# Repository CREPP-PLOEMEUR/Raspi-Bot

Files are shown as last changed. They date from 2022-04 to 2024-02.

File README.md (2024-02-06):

<!--# RaspiBot -->
<!--+ 2016-2017 -->
<!--$ Python-->
<!--$ Arduino -->
<!--$ Bluetooth -->

<!--% Un robot avec retour vidéo et contrôle par Bluetooth -->

# RaspiBot

Un robot avec retour vidéo et contrôle par Bluetooth

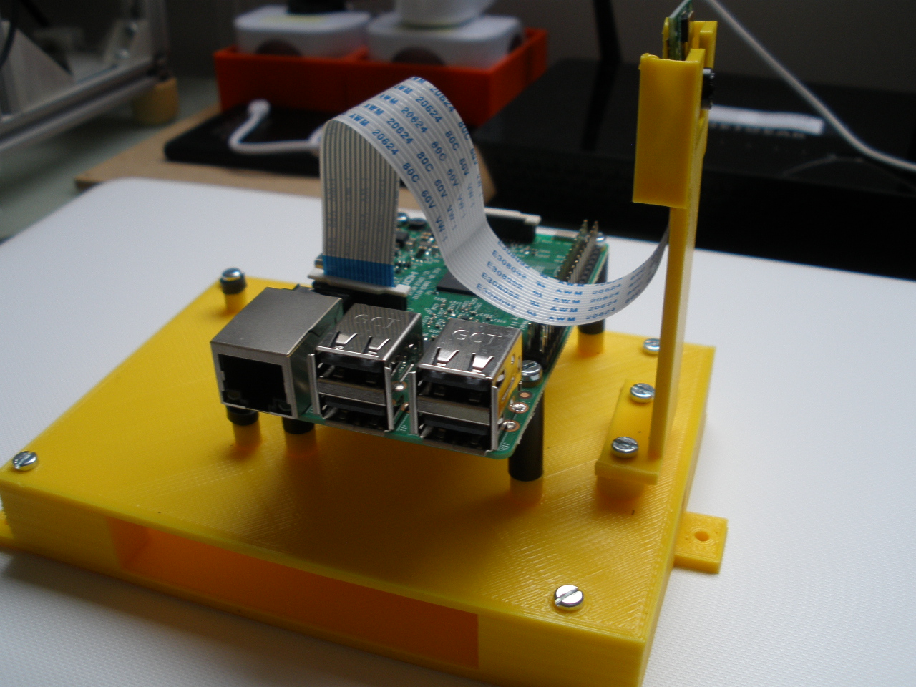
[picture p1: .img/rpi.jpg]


## Sommaire

- Caméra : Toutes les informations sur la caméra et son contrôle

- Code_Arduino : Le code du robot avec les bibliothèques Arduino

- Code_essais : Les codes d'essais des moteurs, caméra...

- Fichiers TSL : Les fichiers STL du projet

- Images : Les images du projet

- Instructions : Les instructions du montage du robot

- Moteurs : les instructions et calculs pour le dimensionnement des moteurs

- 

## Liste du matériel

- 1 ordinateur embarqué Raspberry Pi3 Modèle B 1GB
- 1 Alimentation Micro USB 5V 2,5A pour Raspberry Pi3 et power bank
- 1 Power bank Li-polymer 10000 mAh sorties 1 et 2,1A pour alimentation Rpi3 en autonome
- 1 Module caméra 5MP pour Raspberry Pi3
- 1 carte mémoire microSDHC SanDisk 16 Go, Classe 10

- 1 ensemble support pour Rpi3, carte Arduino et caméra en PLA jaune ( avec visserie et entretoises )

## Informations pratiques

- L'ensemble support avec son Rpi3, sa carte Arduino, sa caméra et la batterie « power bank » sera par la suite intégré au robot roulant.

- La batterie power bank s'insère dans l'espace sous le Rpi3 – carte Arduino. Elle assure l'alimentation de l'ensemble Rpi3-carte Arduino-caméra pour assurer l'autonomie du robot roulant. Son utilisation sera vue par la suite.

- Le support de caméra est provisoire, il sert uniquement à assurer un positionnement en toute sécurité de la caméra pendant les essais.

- Installation de la caméra :

    - Insérer le circuit imprimé dans son support, la nappe vers le bas. 
    - Le connecteur de la carte est celui entre la prise son et la prise hdmi ,noté caméra sur la carte,
    - Relever avec précaution le bloqueur blanc, il se relève de quelques millimètres,
    - Insérer la nappe, contacts vers la prise hdmi, partie bleue vers le port RJ45
    - Ré appuyer sur le bloqueur pour bien fixer.

- L'alimentation ( chargeur ) est utilisée pour alimenter le Rpi3 pour la prise en main du Rpi3 ( installation du logiciel d'exploitation, configuration, chargements des logiciels permettant la prise de contrôle à distance du Rpi3 et du contrôle des flux vidéo sur l'ordinateur distant ).

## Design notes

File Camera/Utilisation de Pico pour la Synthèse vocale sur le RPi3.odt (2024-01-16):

UTILISATION de PICO pour la SYNTHESE VOCALE sur le RPi3

1°- Installer sox :

* Dans le Terminal du RPi3 taper sudo apt-get install sox

2°- Installer Pico :

* Dans le gestionnaire de paquets Synaptic j'ai trouvé libttspico-utils déjà installé.

Quand vous allez dans les propriétés de ce paquet il est dit :

The svox Pico engine is a software speech synthesizer for German, English ( GB and US ), Spanish, French and Italian.

3°- J'ai inséré le scrip en bash suivant écrit par Nicolas dans un fichier lyrics placé dans le dossier Music du RPi3

#!/bin/bash

var="$*"

echo $var

pico2wave -l=fr-FR -w=.fichier.wav "$var" && play .fichier.wav

rm /home/pi/.fichier.wav

4°- Dans le Terminal du RPi3 je tape les cdes suivantes :

a- sudo cp /home/pi/Music/lyrics /bin

b- sudo chmod 777 /bin/lyrics

Puis après avoir mis en service votre émission son sur le RPi3 taper la cde suivante dans le Terminal :

c- lyrics « Ceci est un son généré par Pico »

« Ceci est un son généré par Pico » est appellé « argument ». L'argument peut-être n'importe quelle phrase.

Information :

Il est possible de trouver dans un Carrefour Market des mini HP Bluetooth ( vue par Patrick Pastor ) marque BLUESKY coût : 6,90 €

- Sortie audio 1x1,5w RMS

- Alimentation 5vcc 500mA

- Batterie 3,7vcc 250mAh Lithium-ion

- Autonomie jusqu'à 3,5h

- Temps de recharge minimum 2h environ ( port USB de votre ordinateur )

-Portée du Bluetooh jusqu'à 9,7 m

- Entrée filaire AUX 3,5 mm

Il doit être possible de trouver l'équivalent dans d'autres magasins.

=-=-=-=-=-=

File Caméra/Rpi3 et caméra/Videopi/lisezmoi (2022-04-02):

les vidéos se lancent à l'aide de leurs fichiers .sh respectifs

L'interface mainvideoZ7.py ne sert qu'à en modifier les parametres si cela s'avere necessaire

Ne pas oublier de vérifier pour les fichiers sh ,dans "propriétés/permissions" que la case "autoriser l'execution du fichier comme un programme est bien cochée

même chose pour le fichier d'interface MainvideoZ7.py

Le fichier MainvideoZ7.py se lance avec "executer"

Les fichiers .sh se lancent avec "lancer dans un terminal"

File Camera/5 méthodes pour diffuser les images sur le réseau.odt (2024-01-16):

MagdiBlog

Parce que si on ne se compliquait pas un peu la vie, ce serait beaucoup moins drôle !

MagdiBlog

Aller au contenu

Accueil Sommaire Projets

Pi Home Dash Screen

Pi Car Jukebox

Pi Time Lapse

Pi BOA Drone

BOA Pi Secure Gateway

Domotique GPIO Divers Contact Liens A propos

Magdiblog

Mon CV

RSS

Raspberry Pi Camera – 5 façons de faire du streaming

47 réponses

IMG_8806Le module Raspberry Pi Camera (et la version sans filtre IR, le module NoIR) sont de petits circuits (2,5cm x 2,5cm) dotés d’un capteur photo de 2592 x 1944 pixels capable d’enregistrer en 1080p à 30 images par secondes (ou 60 fps en 720p). Ce module se branche directement sur le port CSI du Pi prévu à cet effet.

La version NoIR permet de voir les infra-rouge, ce qui autorisera une vision nocturne si on le couple à un projecteur infra-rouge comme expliqué à fin de cet article : Système de vidéo-surveillance abordable avec des Raspberry Pi

Que ce soit pour un système de vidéo surveillance ou pour le pilotage d’un robot à distance, il faut pouvoir récupérer le flux vidéo et le diffuser à travers le réseau (streaming). Nous allons voir dans cet article 5 méthodes pour diffuser le flux vidéo d’un module Raspberry Pi Camera, plus ou moins efficacement.

Introduction et matériel utilisé

Le module Raspberry Pi Camera étant branché directement sur un Raspberry Pi, si vous voulez pouvoir voir les images capturées depuis un autre endroit qu’un écran branché sur ce même Pi, vous allez devoir envoyer ces images à travers le réseau. De nombreuses utilisations sont possibles :

la caméra de surveillance que l’on souhaite observer depuis son smartphone quand on part en vacance

le robot que l’on souhaite piloter à distance depuis un ordinateur de contrôle

filmer et diffuser des images en direct à travers internet

etc…

Petit bémol sur la notion de « streaming » vidéo : En principe, lorsqu’on parle de streaming vidéo, il s’agit bien d’un flux vidéo diffusé en direct. Comme nous allons le voir plus loin dans cet article, cette méthode consomme énormément de ressources (notamment en terme de bande passante), et dans de nombreux cas, il sera plus judicieux de diffuser une « suite d’images » à intervalles réguliers.

IMG_8810Le matériel

Pour l’ensemble des méthodes exposées dans cet article, nous utiliserons le matériel et le montage suivant :

Raspberry Pi A+

Module Camera ou la version NoIR

Un dongle WiFi Netgear WNA1000M

Une carte micro-SD SanDisk 8Go

Une batterie Romoss 5200mAh

Le Raspberry Pi A+ est vraiment idéal pour ce genre projet. Découvrez pourquoi en lisant cet article : Raspberry Pi A+ : Le meilleur de tous

On installe une Raspbian, tout ce qu’il y a de plus standard, on se connecte à son réseau WiFi et on active le module caméra grâce à l’outil raspi-config.

Voyons maintenant comment diffuser les images sur le réseau.

Méthode 1 : Netcat et Mplayer

C’est la méthode la plus simple et la plus directe. Il s’agit simplement de rediriger le flux capturé par la commande raspivid dans netcat, puis de récupérer ce flux et l’injecter en entrée dans le lecteur vidéo Mplayer. L’inconvénient de cette méthode est que le flux vidéo n’est visible que depuis un seul PC distant.

Depuis un PC sous Linux exécutez dans un premier temps la commande suivante (après avoir installé mplayer si besoin) :

nc -l -p 5001 | /usr/bin/mplayer -fps 10 -cache 1024 -

Cette commande ordonne à nc (netcat) d’écouter sur le port 5001 et redirige ce qui arrive dans le lecteur vidéo Mplayer en prévoyant un cache de 1024 Ko pour 10 images par secondes.

Puis, sur le Pi, il suffit d’exécuter raspivid et de rediriger la sortie vers l’adresse IP de notre PC client en utilisant netcat :

raspivid -t 0 -w 1280 -h 720 -o - | nc adresse_ip_du_pc_client 5001

On indique ainsi à raspivid de capturer des images en 1280×720 pixels et de les envoyer à netcat.

Simple et efficace, une fenêtre Mplayer s’ouvre automatiquement sur le PC client avec les images en direct. On notera toutefois une forte latence qui peut varier de 3 à 15 secondes en fonction de la qualité et du nombre d’images transmisses et de la qualité du lien WiFi.

Note : Un test réalisé sur un Raspberry Pi B, branché en Ethernet, permet de réduire la latence à environ une seconde.

Si vous souhaitez enregistrer le flux vidéo dans un fichier sur le PC client, il suffit de modifier la première commande de cette manière :

nc -l -p 5001 | /usr/bin/mplayer -fps 10 -cache 1024 -demuxer h264es -dumpstream -dumpfile ./Bureau/ma_video.h264 -

Méthode 2 : streaming VLC

Cette méthode, relativement simple à mettre en place, souffre d’une très forte latence. Toutefois, et contrairement à la première méthode, le flux vidéo est visible depuis plusieurs postes clients.

Sur le Pi, il suffit d’installer VLC :

apt-get install vlc

Puis de rediriger la sortie de la commande raspivid (comme dans la méthode 1) vers VLC en exécutant la commande suivante :

raspivid -t 0 -n --width 1280 --height 720 -o - | cvlc stream:///dev/stdin --sout '#standard{access=http,mux=ts,dst=:8090}' :demux=h264

Coté PC client, il suffit de lire le flux vidéo avec VLC grâce à la commande :

cvlc http://adresse_ip_du_pi:8090

Pour enregistrer le flux vidéo dans un fichier, utilisez la commande suivante :

cvlc http://adresse_ip_du_pi:8090 --sout file/ts:./Bureau/ma_video.h264

Cette méthode est à privilégier si vous souhaitez diffuser votre flux vidéo à plusieurs personnes sur internet par exemple, et que la latence n’est pas un problème.

Méthode 3 : streaming de Pi à Pi avec OMXplayer

Les méthodes 1 et 2 permettent de diffuser le flux vidéo à destination d’un ordinateur distant. Si vous souhaitez capturer un flux vidéo depuis un Pi pour l’observer depuis un autre Pi branché à un écran, il convient d’utiliser le lecteur OMXplayer.

Cette méthode est un peu plus complexe à mettre en oeuvre mais permet plus de souplesse quant à l’usage que l’on souhaite en faire. Depuis le Pi équipé du module caméra, nous allons procéder exactement comme pour la méthode 1, en redirigeant la sortie de la commande raspivid dans netcat. Puis, sur le Pi branché à l’écran de visionnage, nous allons dans un premier temps récupérer le flux netcat pour l’enregistrer dans un fichier et le lire, dans un deuxième temps, avec OMXplayer.

Sur le Pi de visionnage, créez d’abord un fichier de type fifo :

mkfifo /dev/shm/video.fifo

Deux points très important à comprendre dans cette commande :

/dev/shm : ce point montage fonctionne comme un disque dur mais aucune donnée ne sera stockée sur le disque dur en lui même ; tout sera géré en mémoire vive. C’est parfait pour y placer un fichier vidéo tampon.

fichier de type .fifo : les fichiers de type fifo fonctionnent comme les fichiers standards, mais se comportent comme des « pipes », ce qui permet au système d’y stocker des données sans passer par le système de fichier. Encore une fois, parfait pour y placer un fichier vidéo tampon 🙂

Le fichier tampon étant prêt, il faut maintenant le remplir. Côté Pi de visionnage, mettez netcat en écoute en redirigeant la sortie vers le fichier tampon :

nc -l -p 5001 > /dev/shm/video.fifo

Puis côté Pi caméra, envoyez le flux vidéo à travers netcat comme dans la méthode 1 :

raspivid -t 0 -w 960 -h 540 -o - | nc adresse_ip_du_pi_visionnage 5001

De retour sur le Pi de visionnage, il suffit de dire à OMXplayer de lire le fichier tampon :

omxplayer /dev/shm/video.fifo

Cette méthode n’offre pas une latence exemplaire, mais permet de transmettre un flux vidéo de Pi à Pi. Idéal par exemple pour créer un portier vidéo, avec un Pi qui film et un Pi qui affiche la vidéo, les deux Pi étant reliés par WiFi 🙂

Méthode 4 : mjpg-streamer

A partir de là, on sort du streaming vidéo pur et dur puisqu’il s’agit, avec le mjpeg, de transmettre et d’afficher une suite de photos les unes après les autres. Le résultat est beaucoup moins fluide puisqu’on ne pourra espérer afficher que 5 à 10 images par seconde maximum (contre 10 à 30 images par secondes pour les méthodes précédentes), mais nous pourrons exploiter les images beaucoup plus simplement en les affichant dans une page web, ou sur un écran comme le PiHomeDashScreen par exemple. Si vous disposez d’un NAS Synology, ou d’un système sachant gérer des caméras IPs, vous pourrez également exploiter la caméra du Pi grâce à cette méthode.

Voici le lien vers la page SourceForge de mjpg-streamer : http://sourceforge.net/projects/mjpg-streamer/

Dans un premier temps, installez les dépendances de mjpg-streamer ainsi que subversion :

apt-get install subversion

libv4l-dev

libjpeg8-dev

imagemagick

mjpg-streamer aura besoin d’un fichier videodev.sh pour fonctionner correctement :

ln -s /usr/include/linux/videodev2.h /usr/include/linux/videodev.h

Téléchargez ensuite la dernière version de mjpg-streamer grâce à subversion, puis installez le en utilisant les commandes suivantes :

svn co https://svn.code.sf.net/p/mjpg-streamer/code/

cd code/mjpg-streamer

make USE_LIBV4L2=true clean all

make DESTDIR=/usr install

Une fois installé, créez un répertoire temporaire et lancez raspistill en mode timelapse pour capturer 2 images par secondes :

mkdir /tmp/stream

raspistill --nopreview -w 640 -h 480 -q 5 -o /tmp/stream/pic.jpg -tl 500 -t 9999999

Enfin, lancez mjpg-streamer grâce à cette commande :

LD_LIBRARY_PATH=/usr/local/lib mjpg_streamer -i "input_file.so -f /tmp/stream -n pic.jpg" -o "output_http.so -w ./www"

Par défaut, mjpg-streamer lancera un serveur web sur le port 8080/TCP auquel vous pouvez accéder avec un navigateur en utilisant l’adresse : http://adresse_du_pi:8080

Vous devriez voir l’interface de démonstration de mjpg-streamer :

capture_mjpg-streamer

Les deux options les plus intéressantes sont JavaScript et Stream. Ces deux méthodes vous permettrons de récupérer les images pour les afficher dans une page web, ou sur le PiHomeDashScreen comme vous pouvez le voir dans la photo si dessous :

capture_homedashscreen_pi_camera

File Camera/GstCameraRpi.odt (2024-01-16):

# GST :

## commande sur RPI3 IP 192.168.0.29 avec caméra:

/opt/vc/bin/raspivid -t 0 -hf -fps 20 -w 300 -h 300 -o - | gst-lunch-1.0 fdsrc ! h264parse ! rtph264pay config-interval=1 pt=96 ! gdppay ! tcpserversink host=192.168.1.11 port=5000

commande sur Ubuntu :

gst-launch-1.0 -v tcpclientsrc host=192.168.1.11 port=5000 ! gdpdepay ! rtph264depay ! avdec_h264 ! videoconvert ! autovideosink sync=false

commande sur Apple MacBook OS Sierra :

gst-launch-1.0 -v tcpclientsrc host= 192.168.0.29 port=5000 ! gdpdepay ! rtph264depay ! avdec_h264 ! videoconvert ! osxvideosink sync=false

## difficultés rencontrées :

1. Linux Ubuntu 16.04 : aucune !
2. Apple MacBook : installation par brew sous Terminal des paquets suivants :
  1. brew install gstreamer et vérification ok par gst-inspect-1.0 (si problème avec le Python natif Apple, brew unlink python / brew link –overwrite python/ brew install gstreamer)
  2. brew install gst-plugins-base
  3. brew install gst-libav
  4. brew install gst-plugins-ugly
  5. brew install gst-plugins-bad
  6. brew install gst-plugins-good
3. impossible de lire le flux gst sur Apple MacBook VLC

(peut-être que pour Microsoft Windows,

mplayer -fps 200 -demuxer h264es ffmpeg://tcp://192.168.0.29:5000

et il faudra peut-être installer plusieurs bibliothèques complémentaires

## impressions

très rapide, pas de latence

# SON

Achat d'un petit haut parleur Bluetooth + fil à Carrefour Ploemeur : moins de 9€ !

pico2wave -l fr-FR -w bonjour.wav « Bonjour le monde »

installation de sox :

sudo apt-get install sox

Terminal/ ligne de commande :

play bonjour.wav

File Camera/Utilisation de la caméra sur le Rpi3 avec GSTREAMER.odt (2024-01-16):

UTILISATION de la CAMÉRA sur le RPi3 avec GSTREAMER

1°- Installer GSTREAMER sur le RPi3 et son PC client :

* Aller dans Gestionnaire de paquets Synaptic

* Rechercher gstreamer1.0

Ensuite, comme je n'y connais pas grand chose, j'ai installé tous les paquets en commençant par :

gstreamer1.0-alsa ….les spécialistes sauront faire leur choix.

2°- Dans un fichier ad hoc sauvegardé sur le bureau du RPi3, écrire la cde suivante que l'on appellera « Commande émission caméra » ( origine Patrick Pastor ) :

/opt/vc/bin/raspivid -t 0 -hf -fps 20 -w 300 -h 300 -o - | gst-launch-1.0 fdsrc ! h264parse ! rtph264pay config-interval=1 pt=96 ! gdppay ! tcpserversink host= adresse IP du RPi3 port=5000

3°- Dans un fichier ad hoc sauvegardé sur le bureau du Pc client, écrire la cde suivante que l'on appellera « Commande réception image » ( origine Patrick Pastor ) :

gst-launch-1.0 -v tcpclientsrc host= adresse IP du Rpi3 port=5000 ! gdpdepay ! rtph264depay ! avdec_h264 ! videoconvert ! autovideosink sync=false

4°- Mise en œuvre :

* Après avoir pris le contrôle du RPi3 par le Pc client :

a- Copier-coller dans le Terminal du RPi3 la ligne de cde du fichier ad hoc. La diode rouge de la caméra s'allume, la caméra est en service.

b- Copier-coller dans le Terminal du Pc client la ligne de cde du fichier ad hoc,

c- Taper Enter ( clavier du PC client ) L'écran de la caméra s'affiche sur le bureau du Pc client.

* Si l'on souhaite modifier les dimensions de cet écran, intervenir dans la ligne de cde émission caméra du Rpi3 au niveau de -w et -h,

* On peut également agir sur le nombre d'images par seconde au niveau de -fps.

Remarques :

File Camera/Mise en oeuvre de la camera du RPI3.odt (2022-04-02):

MISE en OEUVRE de la CAMÉRA du Rpi3

RPi3 sous Jessie (Debian) et PC client sous Linux

=-=-=-=-=-=-=

MÉTHODE GSTREAMER :

I- Installer gstreamer1.0 dans le Rpi3 et le PC client :

* Ouvrir Synaptic ( si ce gestionnaire de paquets n'est pas installé taper dans les Terminaux du Rpi3 et du PC client ) sudo apt-get install synaptic

* Si Synaptic est installé, dans les Terminaux taper sudo apt-get update

- Cliquer sur Rechercher,

- Dans la fenêtre qui apparaît taper gstreamer1.0 puis cliquer sur Rechercher,

- Dans la liste des paquets qui apparaît, les paquets déjà installés sont signalés par un petit carré vert,

- Les paquets suivants doivent être installés de façon exhaustive :

- gstreamer1.0-alsa

- gstreamer1.0-clutter-3.0

- gstreamer1.0-libav

- gstreamer1.0-nice

- gstreamer1.0-plugins-bad

- gstreamer1.0-plugins-base

- gstreamer1.0-good

- gstreamer1.0-ugly

- gstreamer1.0-tools

- gstreamer1.0-x

- libgstreamer1.0-0

Pour installer un paquet :

* Sélectionner le paquet,

* Dans la fenêtre « Prévoir d'effectuer d'autres changements » cliquer sur A installer puis sur Ajouter à la sélection,

* Cliquer sur Appliquer ( dans la ligne en haut à côté de Propriétés),

* Dans la fenêtre qui apparaît « Appliquer les modifications suivantes ? » cliquer sur Installer puis sur Appliquer.

Remarques :

1°- Dans le cas où on vous signale que pour une liste de paquets certains sont cassés, aller dans « Edition » et cliquer sur Réparer les paquets cassés.

2°- Si dans le petit carré vert d'un paquet installé il y a un astérisque ou une autre marque jaune, sélectionner ce paquet et le mettre à jour.

II- Mise en service de la caméra et capture de la vidéo :

2-1 Installer les fichiers « Lignes de commande » :

* Sur le bureau du PC client : GST Cde camera sur PC client.odt

* Sur le bureau du Rpi3 : GST Cde sur Rpi3 de la camera.odt

Important : vérifier que l'adresse IP est bien celle du Rpi3 dans les 2 cas.

2-2 Sur le Rpi3 :

* Ouvrir GST Cde sur Rpi3 de la camera .odt et copier la ligne de cde.

* Dans le Terminal du Rpi3 coller cette ligne de cde. La diode rouge de la caméra s'allume.

2-3 Sur le PC client :

* Ouvrir GST Cde camera sur PC client.odt et copier la ligne de cde.

* Dans le Terminal du PC client coller cette ligne de cde

* Enter

Déroulement de lignes de programmme dans le Terminal puis un écran vidéo s'affiche avec une image pratiquement sans latence.

=-=-=-=-=-=-=

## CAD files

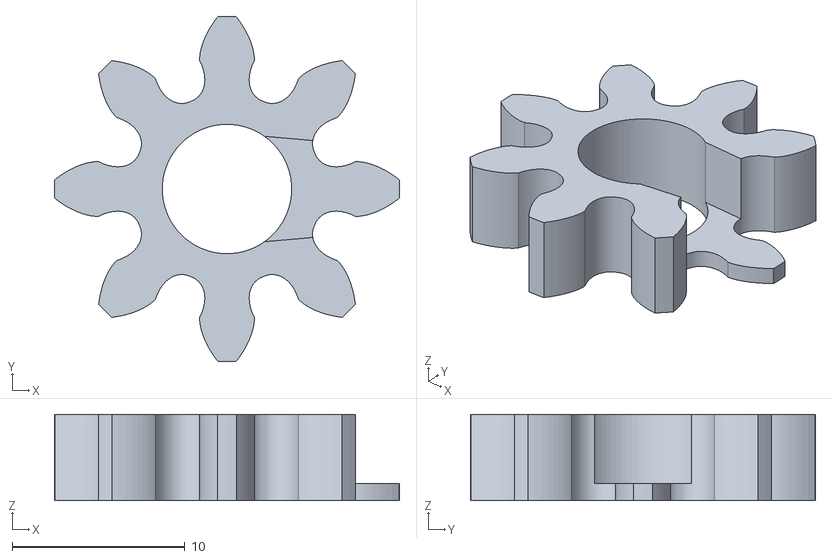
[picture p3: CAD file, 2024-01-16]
EEZYbotARM/EEZYbotARM ok.stl/EBA_01.00.015_drive_gear.STL
20.0 x 20.0 x 5.00

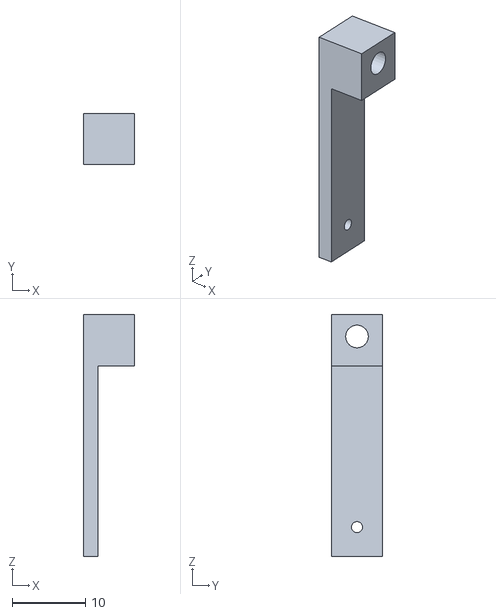
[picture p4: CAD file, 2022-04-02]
fichiers STL/Pan tilt/bielle1.stl
7.00 x 7.00 x 33.0

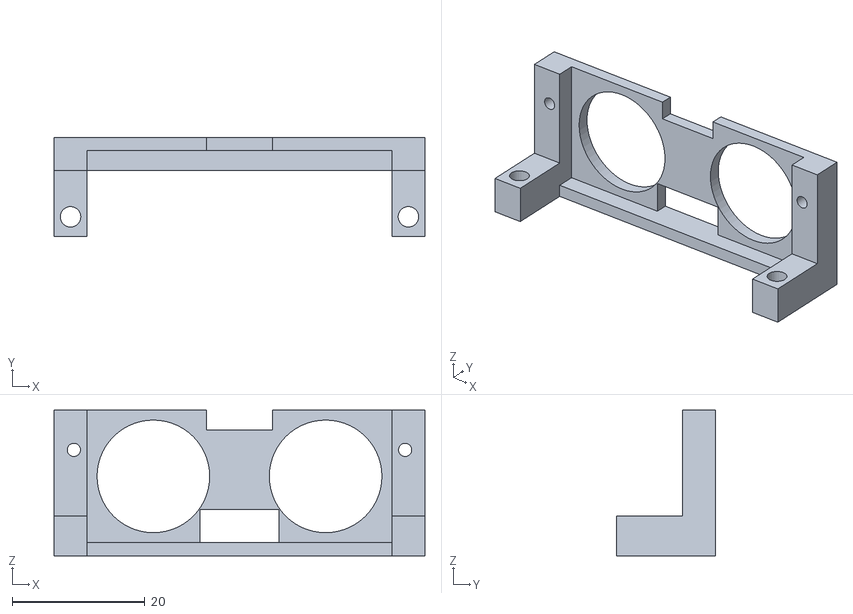
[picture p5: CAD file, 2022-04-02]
fichiers STL/ultrason2.stl
56.0 x 15.0 x 22.0

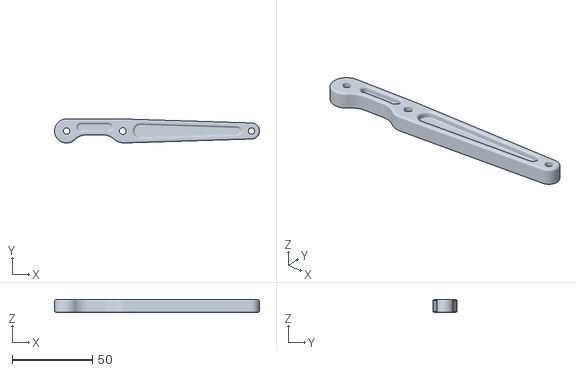
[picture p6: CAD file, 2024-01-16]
EEZYbotARM/EEZYbotARM ok.stl/EBA_01.00.005_horizontal_arm.STL
127.5 x 15.0 x 8.00

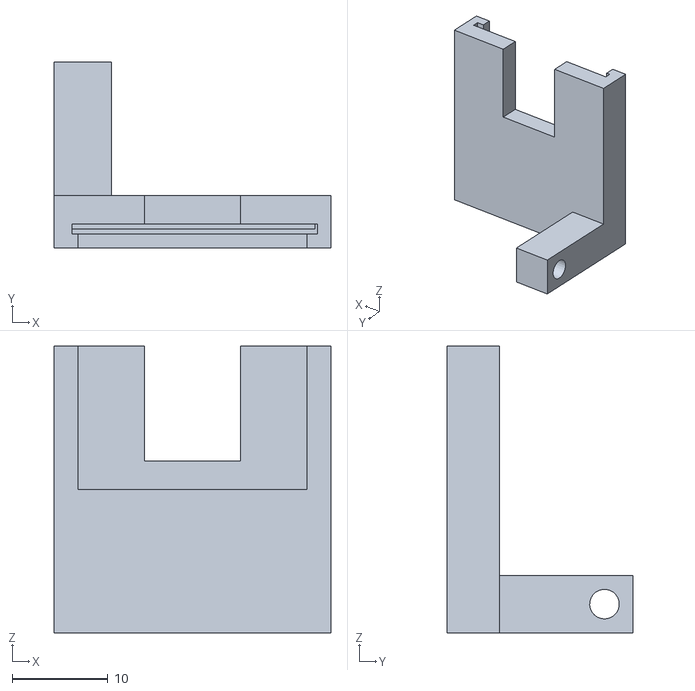
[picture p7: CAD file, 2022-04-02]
fichiers STL/Pan tilt/supportCam.stl
29.0 x 19.5 x 30.0

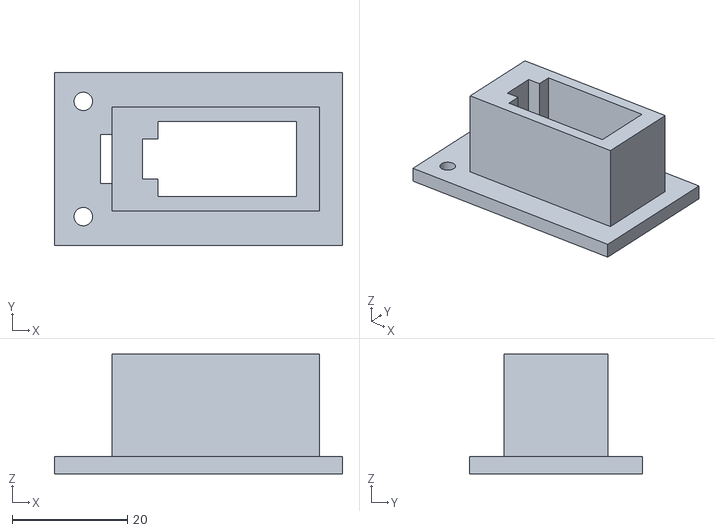
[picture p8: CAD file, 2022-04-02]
fichiers STL/Support pivotant camera Rpi3.stl
50.0 x 30.0 x 20.8

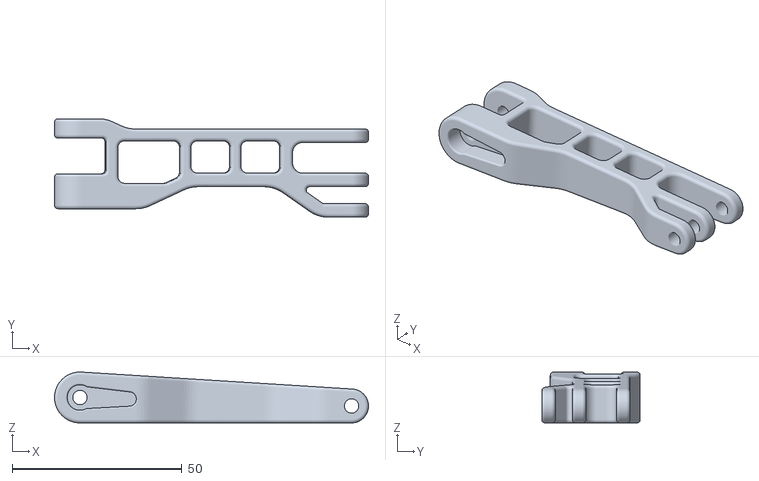
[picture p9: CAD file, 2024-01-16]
EEZYbotARM/EEZYbotARM ok.stl/EBA_01.00.004_forward_drive_arm.STL
92.5 x 29.0 x 15.0

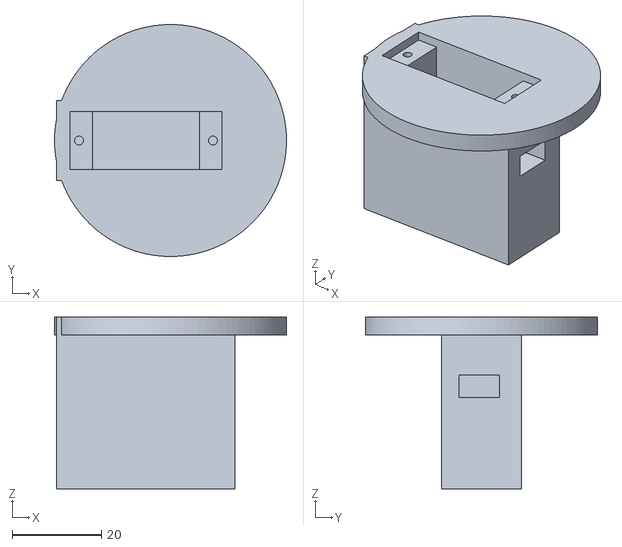
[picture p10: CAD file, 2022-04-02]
fichiers STL/Pan tilt/Socle.stl
52.0 x 52.0 x 38.5

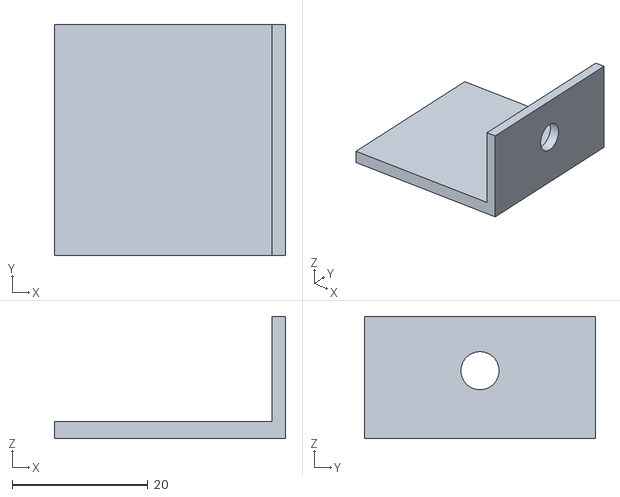
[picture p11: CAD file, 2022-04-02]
fichiers STL/support inter bat 9vscad.stl
34.0 x 34.0 x 18.0

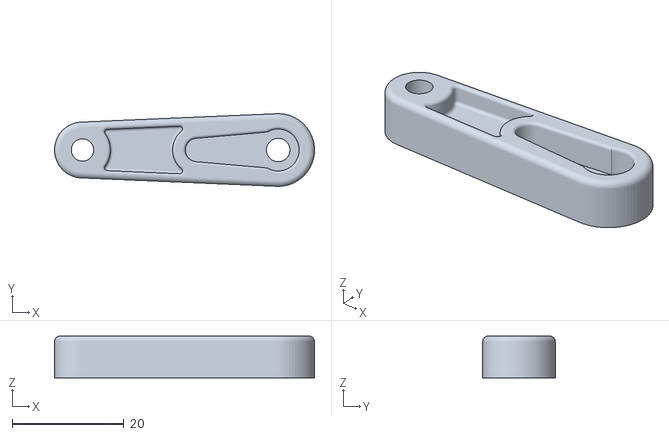
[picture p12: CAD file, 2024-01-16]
EEZYbotARM/EEZYbotARM ok.stl/EBA_01.00.002_vertical_drive_arm.STL
46.5 x 13.0 x 7.50

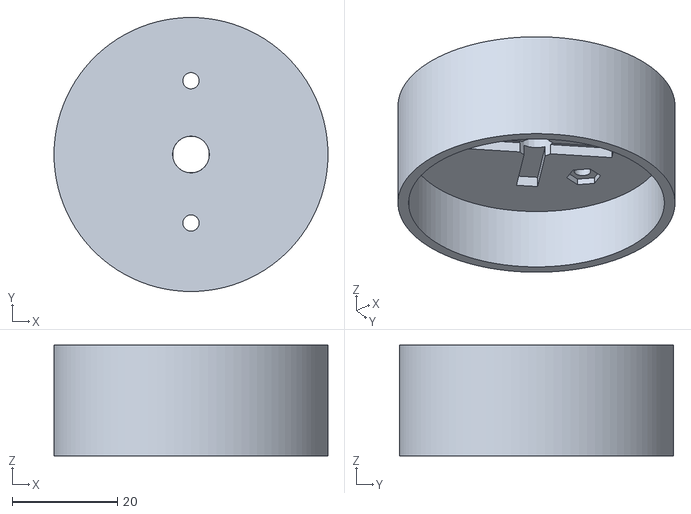
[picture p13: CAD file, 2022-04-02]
fichiers STL/Pan tilt/BaseTournante.stl
52.0 x 52.0 x 21.0

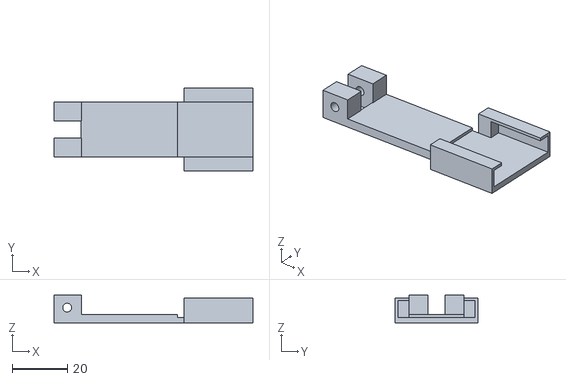
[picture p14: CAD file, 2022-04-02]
fichiers STL/Support camera Rpi3 pivotant.stl
72.3 x 30.0 x 10.0

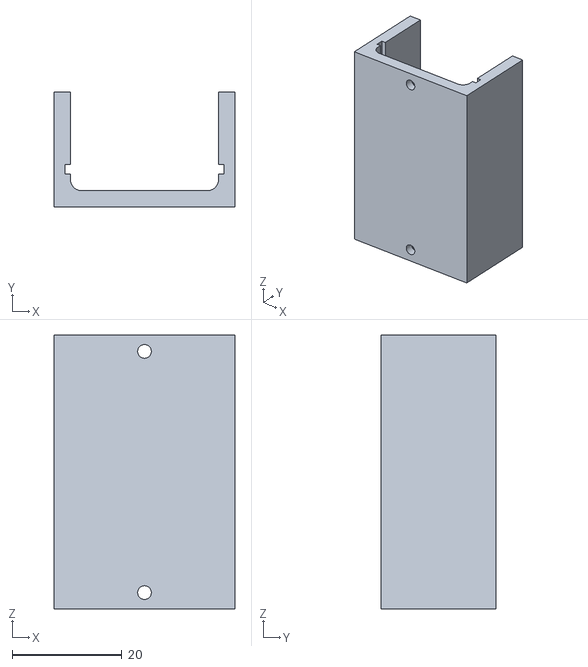
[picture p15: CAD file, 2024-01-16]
EEZYbotARM/EEZYbotARM ok.stl/EBA_01.00.018_maestro_holder.STL
33.0 x 21.0 x 50.0

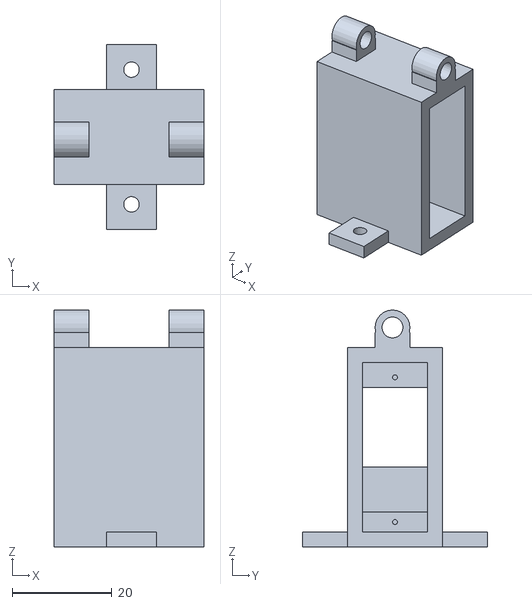
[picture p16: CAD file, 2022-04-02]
fichiers STL/Pan tilt/Cagehaut.stl
30.0 x 37.0 x 47.5

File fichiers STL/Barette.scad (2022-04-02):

cube([70,10,4],center=true);

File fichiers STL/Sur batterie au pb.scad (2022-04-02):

difference() {
cube([155,98,15],center=true);
    translate([0,0,2.5])cube([151,94,15],center=true);
    translate([-58,-49,0])cube([40,8,15],center=true);
    translate([58,-49,0])cube([40,8,15],center=true);
    
}

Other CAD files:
fichiers STL/Support pour pos verticale.stl
EEZYbotARM/EEZYbotARM ok.stl/EBA_01.00.017_R01_ramp.STL
fichiers STL/Pan tilt/Pivot.stl
fichiers STL/Sur batterie au pb.stl
EEZYbotARM/EEZYbotARM ok.stl/EBA_01.00.001.STL
EEZYbotARM/EEZYbotARM ok.stl/EBA_01.00.003_link.STL
EEZYbotARM/EEZYbotARM ok.stl/EBA_01.00.006_triangular_link.STL
EEZYbotARM/EEZYbotARM ok.stl/EBA_01.00.009_servo_plate.STL
EEZYbotARM/EEZYbotARM ok.stl/EBA_01.00.010_basement.STL
EEZYbotARM/EEZYbotARM ok.stl/EBA_01.00.011_round_plate.STL
EEZYbotARM/EEZYbotARM ok.stl/EBA_01.00.012_R01_claw_support.STL
EEZYbotARM/EEZYbotARM ok.stl/EBA_01.00.013_R01_right_finger.STL
EEZYbotARM/EEZYbotARM ok.stl/EBA_01.00.014_R01_left_finger.STL
EEZYbotARM/EEZYbotARM ok.stl/EBA_01.00.016_R01_driven_gear.STL
EEZYbotARM/EEZYbotARM ok.stl/EBA_01.00.019_ball.STL
fichiers STL/Banc essais servos.stl
fichiers STL/Barette.stl
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

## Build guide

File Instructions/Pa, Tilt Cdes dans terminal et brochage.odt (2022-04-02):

PROGRAMME de cde moteurs, pan-tilt, bras articulé

Ordre des cdes à insérer dans le Terminal Arduino :

vitMG,vitMD,sensMG,sensMD,RotCam,ÉlevCam,RotBras,ÉlevBras,AvArBras,PinceBras

Brochage :

0 Réserve téléversement/communication

1 Réserve téléversement/communication

2 Servomoteur rotation caméra

3 Servomoteur haut/bas caméra

4 Moteur M1 (gauche) sens moteur

5 Moteur E1 (gauche) vitesse pwm

6 Moteur E2 (droit) vitesse pwm

7 Moteur M2 (droit) sens moteur

8 Bras servo base (rotation)

9 Bras servo Avant / Arrière

10 Bras servo élévation

11 Bras servo pince

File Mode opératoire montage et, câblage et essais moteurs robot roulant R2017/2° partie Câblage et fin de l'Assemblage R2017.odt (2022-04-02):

2 ème partie

CÂBLAGE et fin de l' ASSEMBLAGE

Robot roulant 2016-2017

1°- VUES d' ENSEMBLE du robot roulant 2016-2017 :

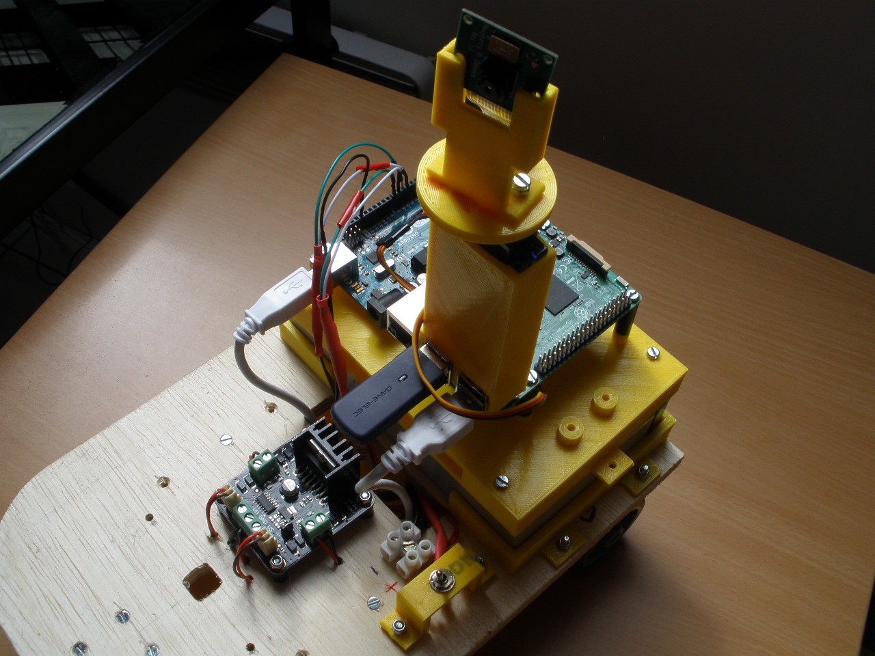
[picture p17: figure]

Photo n° 1

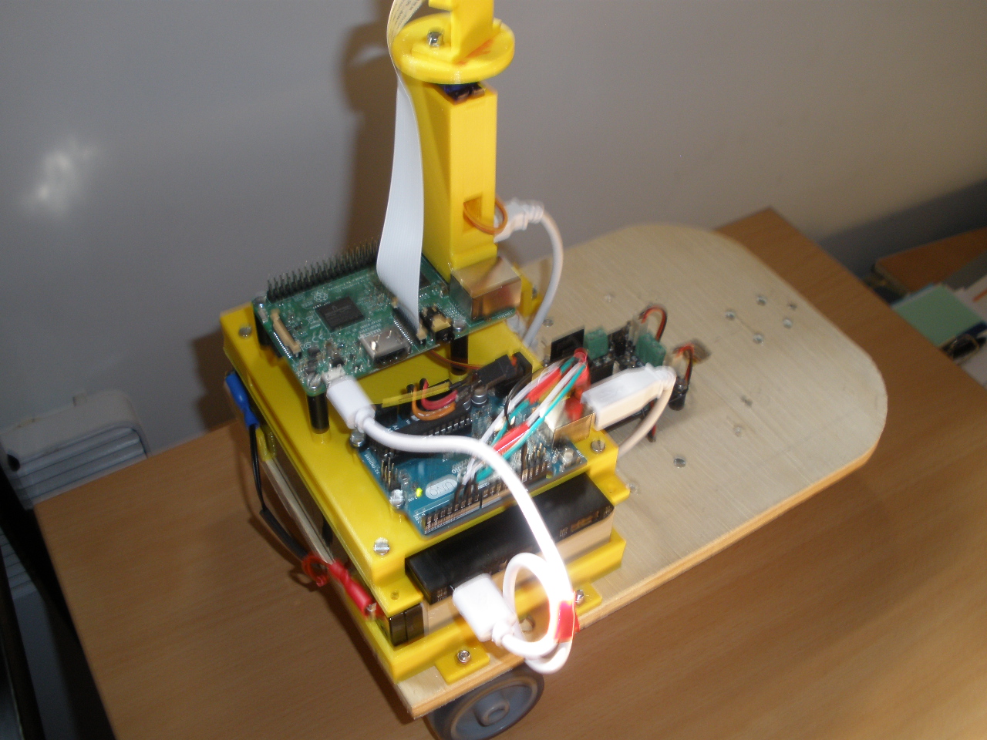
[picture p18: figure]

Photo n° 2

Liaison sortie 2.1A batterie lithium et port mini USB du Rpi3.

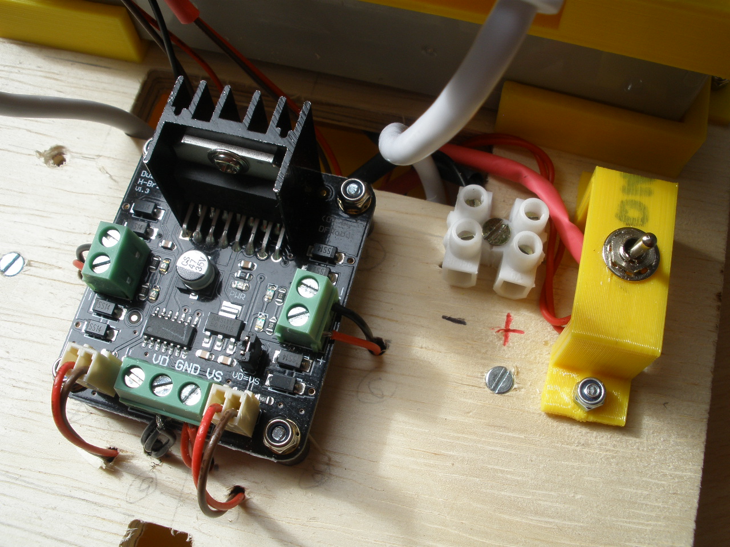
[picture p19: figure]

Photo n° 3

Module de cde, domino et interrupteur.

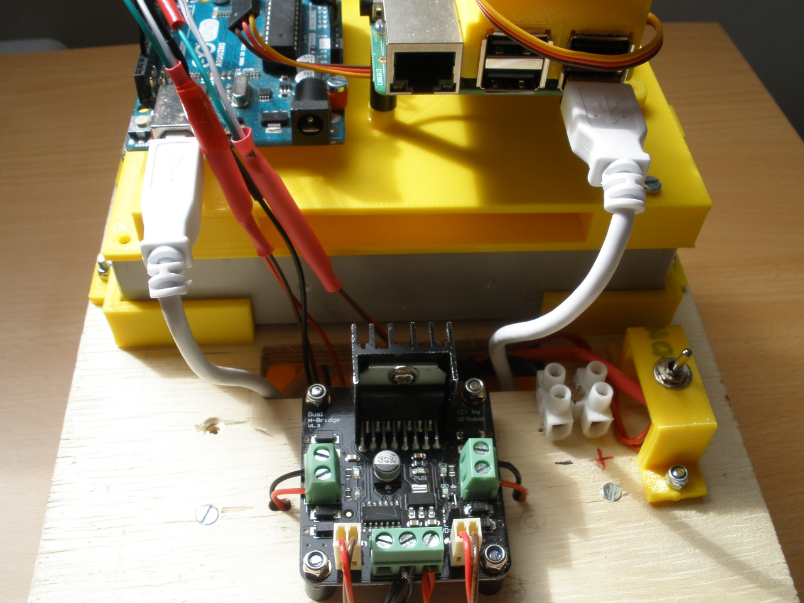
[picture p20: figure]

Photo n°4

Liaison par cordon USB entre le port USB de la carte Arduino et un des ports USB du Rpi3.

2°- ORDRE des OPÉRATIONS à EFFECTUER :

2-1 Câblage suivant le schéma de câblage ( dossier Mode opératoire montage et câblage ⇒ Schéma d'alimentation du module de cde DR10002 ).

a) - Relier le + batterie au pb à la broche milieu de l'interrupteur,

- Relier l'un des 2 autres plots de l'interrupteur à l'une des bornes du domino ( nous l'appellerons + ),

- Relier le – de la batterie au plomb à l'autre borne du domino ( nous l'appellerons - ).

b) – Relier la borne + du domino ( déjà occupée par la liaison interrupteur ) à la borne VS du module de commande,

- Relier la borne – du domino ( déjà occupée par la liaison – batterie ) à la borne GND du module de commande.

c) – Relier la borne – du domino ( déjà occupée par la liaison – batterie et la liaison module de cde ) au plot GND côté port USB de la carte Arduino.

d) – Liaisons moteurs-module de commande :

Relier la broche + du moteur gauche au plot + M1 du module de cde,

Relier la broche – du moteur gauche au plot – M1 du module de cde,

Relier la broche + du moteur droit au plot + M2 du module de cde,

Relier la broche – du moteur droit au plot – M2 du module de cde.

e) – Liaisons Arduino module de commande : Les pins choisis de la carte Arduino correspondent au programme « essais moteurs » ( dossier Mode opératoire montage et câblage ⇒ Module de cde DR10002 ⇒ Module de cde DR10002 code ).

Relier : E1 M1 et E2 M2 bornes du module de cde. 4, 5, 6, 7 pins Arduino

E1 ⇒ pin 4

M1 ⇒ pin 5

E2 ⇒ pin 7

M2 ⇒ pin 6

2-2 Relier la carte Rpi3 à la carte Arduino à l'aide du cordon USB ( photo n° 4 )

FIN de la 2ème PARTIE

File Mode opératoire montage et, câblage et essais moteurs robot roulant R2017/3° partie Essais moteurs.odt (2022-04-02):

3 ème partie

ESSAIS des MOTEURS CC

Robot roulant 2016-2017

Ces essais se feront directement avec votre ordinateur personnel

1°- Relier votre ordinateur à l'aide du cordon USB ( kit Arduino ) à la carte Arduino,

2°- Ouvrir le logiciel Arduino,

3°- copier-coller le code suivant dans la fenêtre du logiciel Arduino

int E1 = 5;

int M1 = 4;

int E2 = 6;

int M2 = 7;

void setup()

{

pinMode(M1, OUTPUT);

pinMode(M2, OUTPUT);

}

void loop()

{

int value;

for(value = 0 ; value <= 255; value+=5)

{

digitalWrite(M1,HIGH);

digitalWrite(M2,HIGH);

analogWrite(E1, value); //PWM Speed Control

analogWrite(E2, value); //PWM Speed Control

delay(30);

}

}

Après vérification, téléverser ce code dans la carte Arduino ...les moteurs doivent tourner en marche AV. Si l'un d'eux tourne en sens inverse, inverser sa liaison avec le module de cde.

FIN de la 3 ème PARTIE

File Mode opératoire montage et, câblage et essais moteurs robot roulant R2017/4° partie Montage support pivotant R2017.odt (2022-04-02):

4 ème partie

MONTAGE des ÉLÉMENTS du SUPPORT ORIENTABLE de la CAMÉRA

Robot roulant 2016-2017

=-=-=-=-=

1°- LES 2 ÉLÉMENTS du SUPPORT :

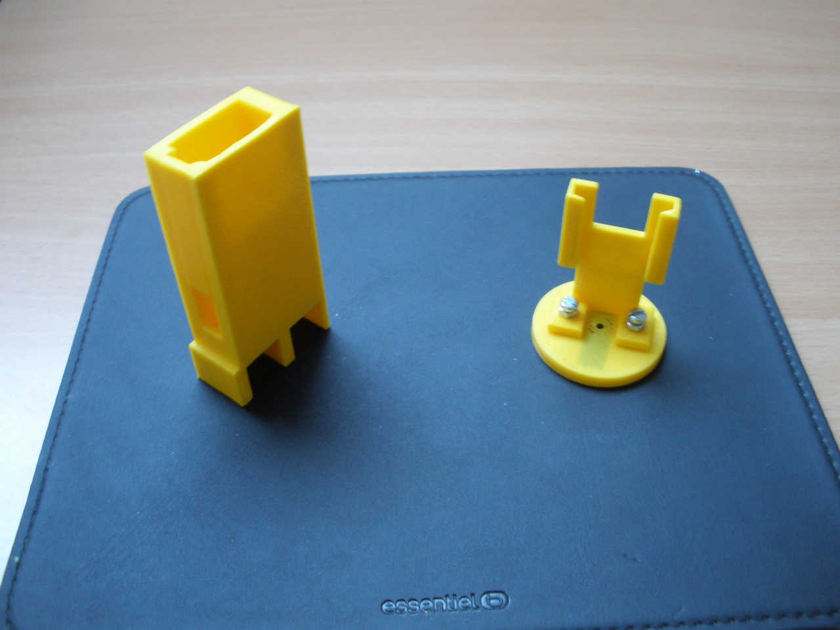
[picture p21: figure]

A gauche la partie fixe et à droite la partie mobile.

2°- COLLER le PALONNIER du servomoteur sous l'un des éléments du support de caméra :

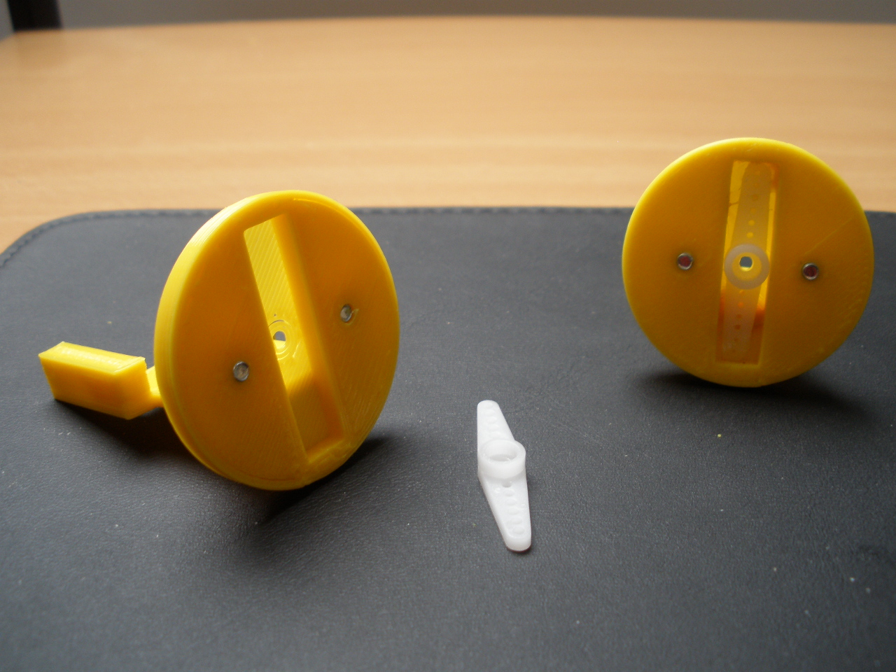
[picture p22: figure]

Utiliser une colle contact type gel. Ici colle Pattex, déposer sur les 2 extrémités de la rainure dans la pièce ronde et les 2 extrémités du palonnier une goutte de colle, laisser sécher 15 mn, placer le palonnier dans la rainure et presser pendant 5 secondes.

3°- PLACER le SERVOMOTEUR dans son support fixe :

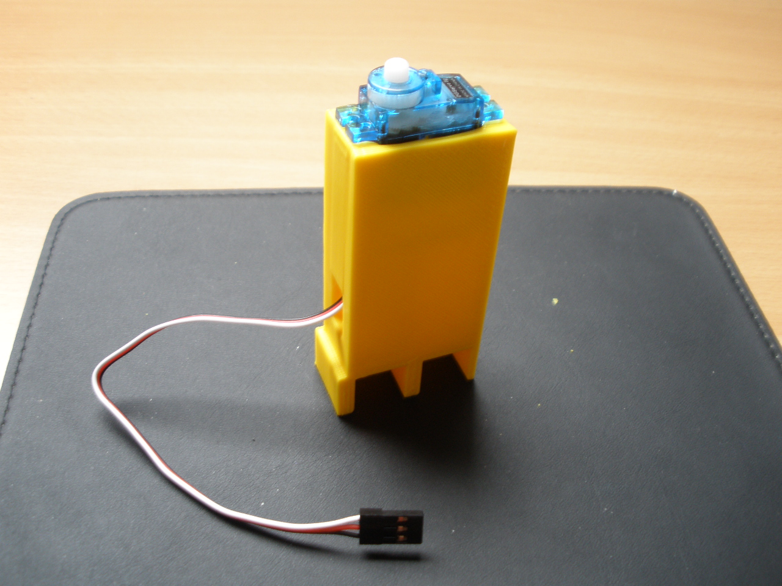
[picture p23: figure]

3-1- Introduire le câble de liaison du servo par la partie supérieure du support fixe et le faire sortir par l'ouverture au bas du support.

3-2-Insérer légèrement en force le servo dans son logement, axe moteur à gauche suivant image ci-dessus.

4°- FIXER le support de la caméra sur le servomoteur :

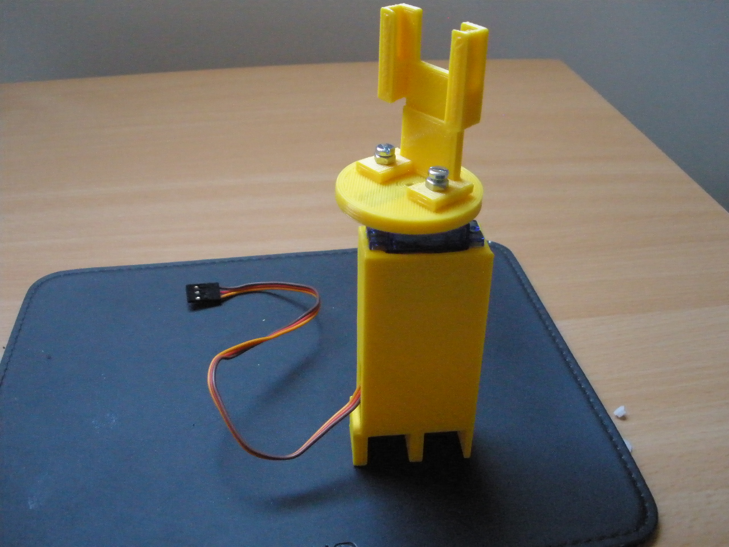
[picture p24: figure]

Introduire la partie femelle crénelée du palonnier du support de caméra sur l'axe crénelé du servomoteur. Visser l'ensemble à l'aide de l'une des petites vis fournies avec le servomoteur ( différents palonniers et vis ).

Ceci n'est pas une fixation définitive, elle se fera plus tard lors des essais.

5°- FIXER l' ENSEMBLE sur le Rpi3 :

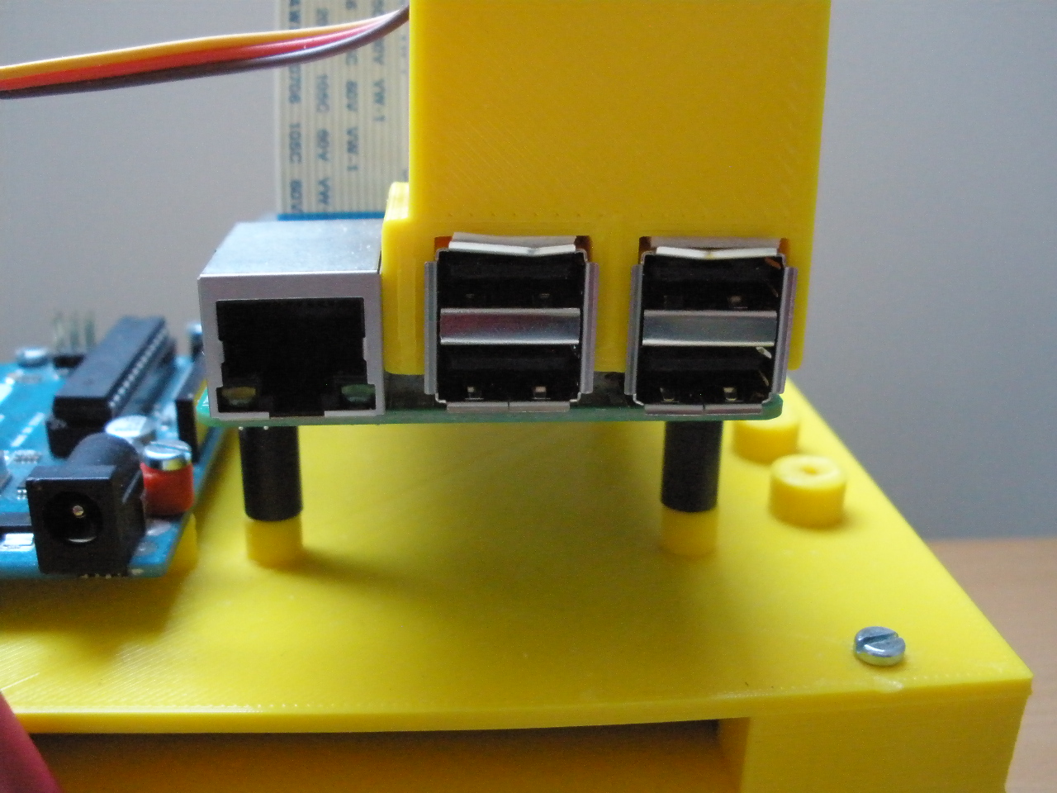
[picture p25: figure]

5-1- Coller un petit rectangle de scotch double face sur la partie supérieure des 2 ports USB du Rpi3,

5-2- Insérer l'ensemble comme indiqué sur l'image ci-dessus.

FIN de la 4 ème PARTIE

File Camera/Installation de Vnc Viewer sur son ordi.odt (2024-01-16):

INSTALLATION de VNC VIEWER

sur votre ordinateur « LINUX »

VNC pour Virtual Network Computing est un système de pilotage d'ordinateur à distance.

- Votre pc embarqué Rpi3 est l'ordinateur serveur, le logiciel VNC Server est déjà installé.

- Votre ordinateur personnel est l'ordinateur client, il vous faudra installer le logiciel VNC Viewer.

INSTALLATION de VNC Viewer :

1°- Dans un moteur de recherche ⇒ Real VNC

2°- Cliquer sur RealVNC | the original and best for remote……

3°- Une fenêtre apparaît « Connect & take control » et 2 possibilités :

- Grand écran ( ordi portable ) cliquer sur « Download »,

- Petit écran ( eeePC, note book ) cliquer sur « ≡ » puis sur « Download »

4°- Dans la ligne des icônes cliquer au choix sur Windows ou Mac OS x ou Linux.

5°- Sous Download VNC Connect 6.0.0 choisir dans le menu déroulant DEB x86 ou DEB x64

6°- Télécharger

7°- Dans votre dossier « Téléchargements » ⇒ clic droit sur VNC-6.0.0-Linux-x86-DEB.tar.gz

puis clic sur « Extraire ici »

et ouvrir VNC-6.0.0-Linux-x86-DEB

8°- 2 fichiers VNC Server et VNC Viewer

Ouvrir VNC Viewer avec la Logithèque Ubuntu ou G Debi

Il est possible qu'il y ait conflit avec le logiciel xtightvncviewer qui aurait été préalablement installé. Aller dans le Terminal et taper la ligne de code sudo apt-get xtightvncviewer remove.

9°- Aller dans le menu des applications :

cliquer sur « Internet »

cliquer sur « VNC Viewer »

Dans la fenêtre VNC Viewer entrer l'adresse IP de votre Raspberry Pi3

RECHERCHE de l' ADRESSE IP du Rpi3 :

Dans un lieu donné cette adresse va dépendre du réseau wifi et du nombre d'appareils raccordés à ce réseau.

1°- Recherche de l'adresse IP du Rpi3 par votre PC :

- Dans le Terminal de votre PC taper la ligne de code sudo nmap -sP 192.168.10.0-255

- Relever les différentes adresses

2°- Dans le menu déroulant des applications :

- Cliquer sur « Internet » dans ce menu :

- Cliquer sur « VNC Viewver »

3°- Dans la fenêtre VNC Viewer :

- Entrer l'une des adresses IP que vous avez relevées précédemment

- « Enter »

On vous demande :

- votre username taper pi

- votre mot de passe taper raspberrypi

- taper OK

On voit apparaître l'écran du Rpi3 sur l'écran de votre PC

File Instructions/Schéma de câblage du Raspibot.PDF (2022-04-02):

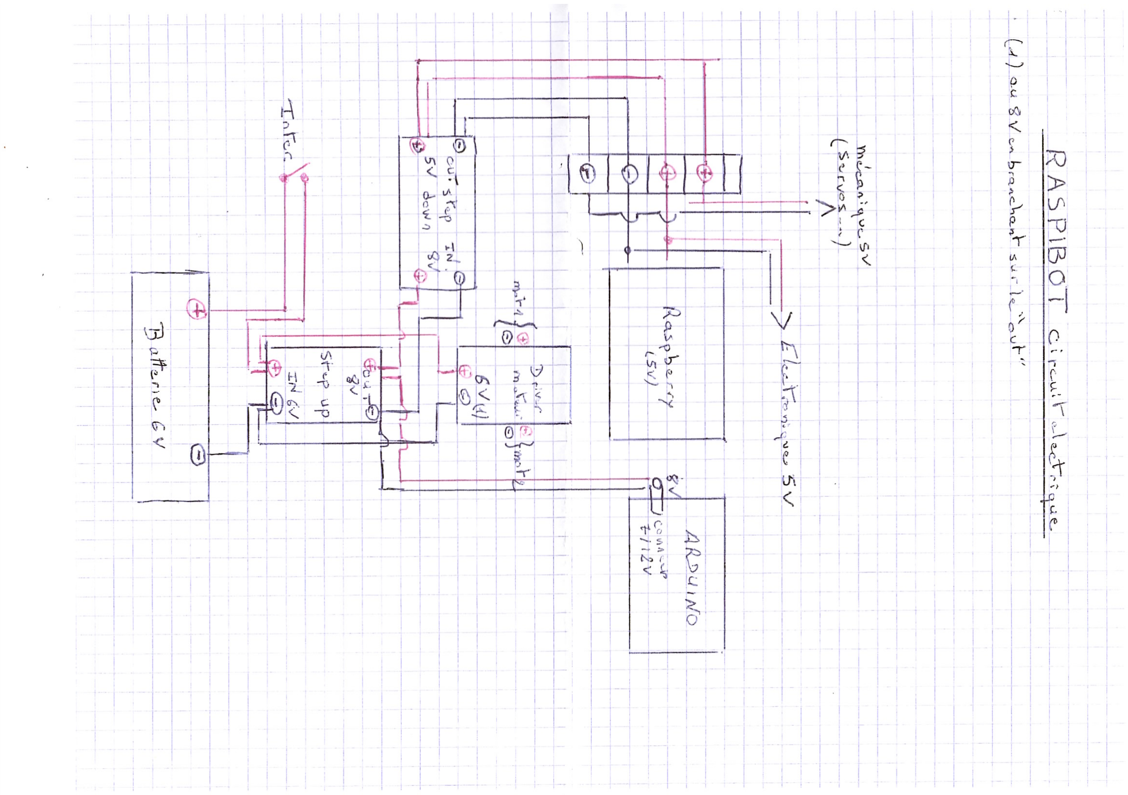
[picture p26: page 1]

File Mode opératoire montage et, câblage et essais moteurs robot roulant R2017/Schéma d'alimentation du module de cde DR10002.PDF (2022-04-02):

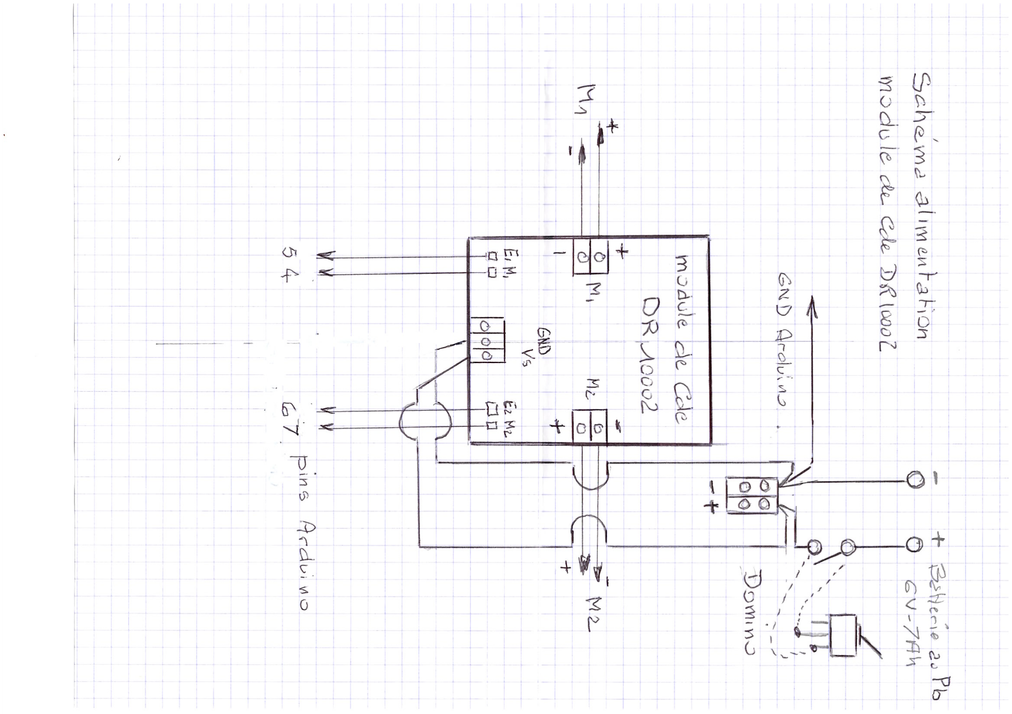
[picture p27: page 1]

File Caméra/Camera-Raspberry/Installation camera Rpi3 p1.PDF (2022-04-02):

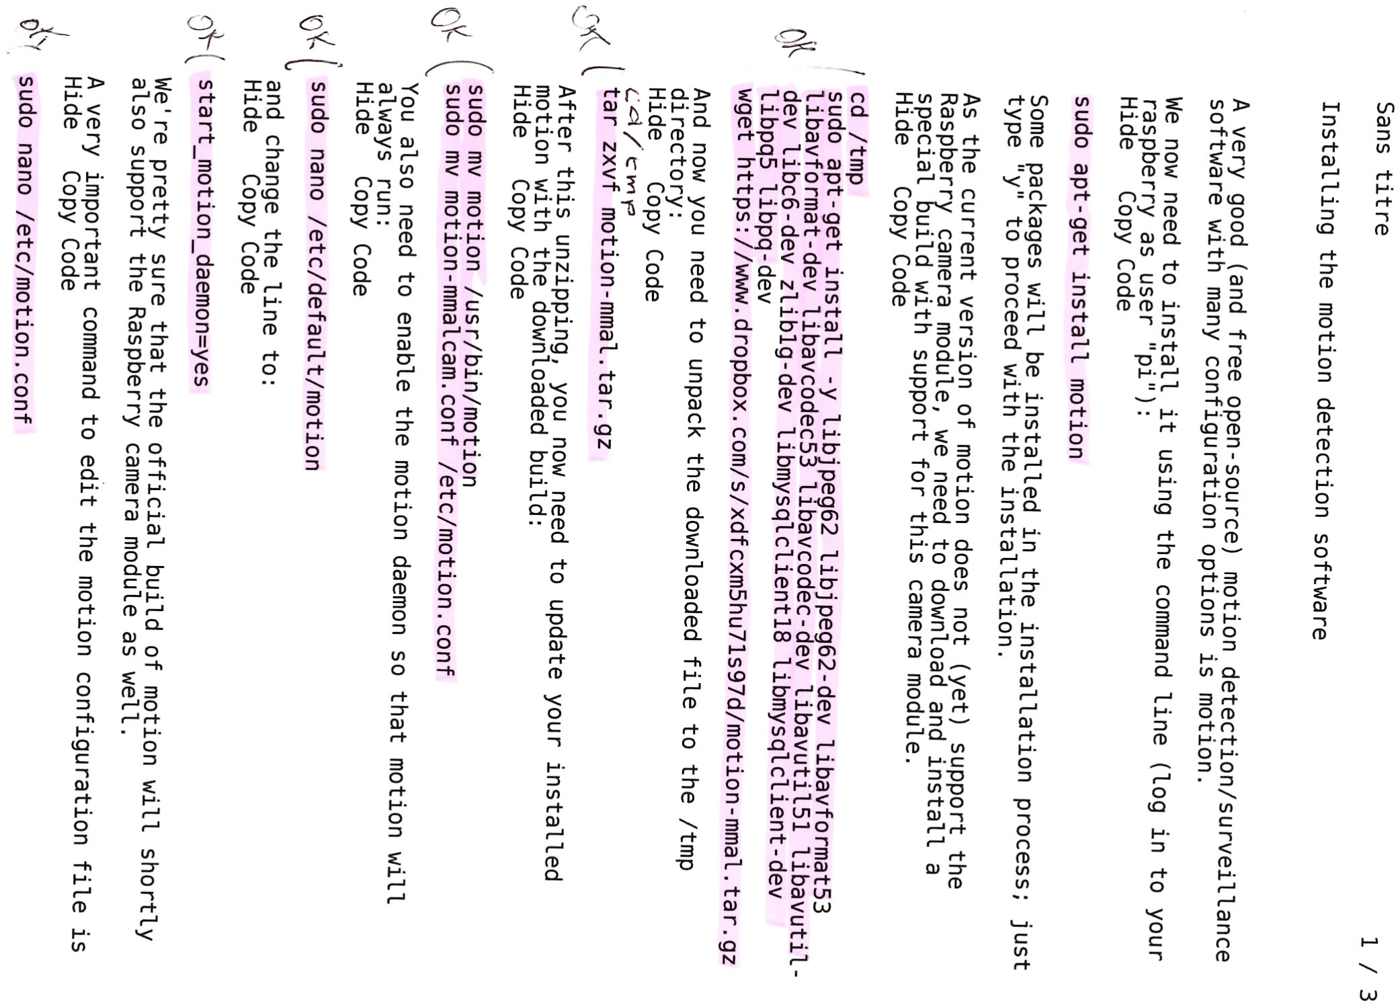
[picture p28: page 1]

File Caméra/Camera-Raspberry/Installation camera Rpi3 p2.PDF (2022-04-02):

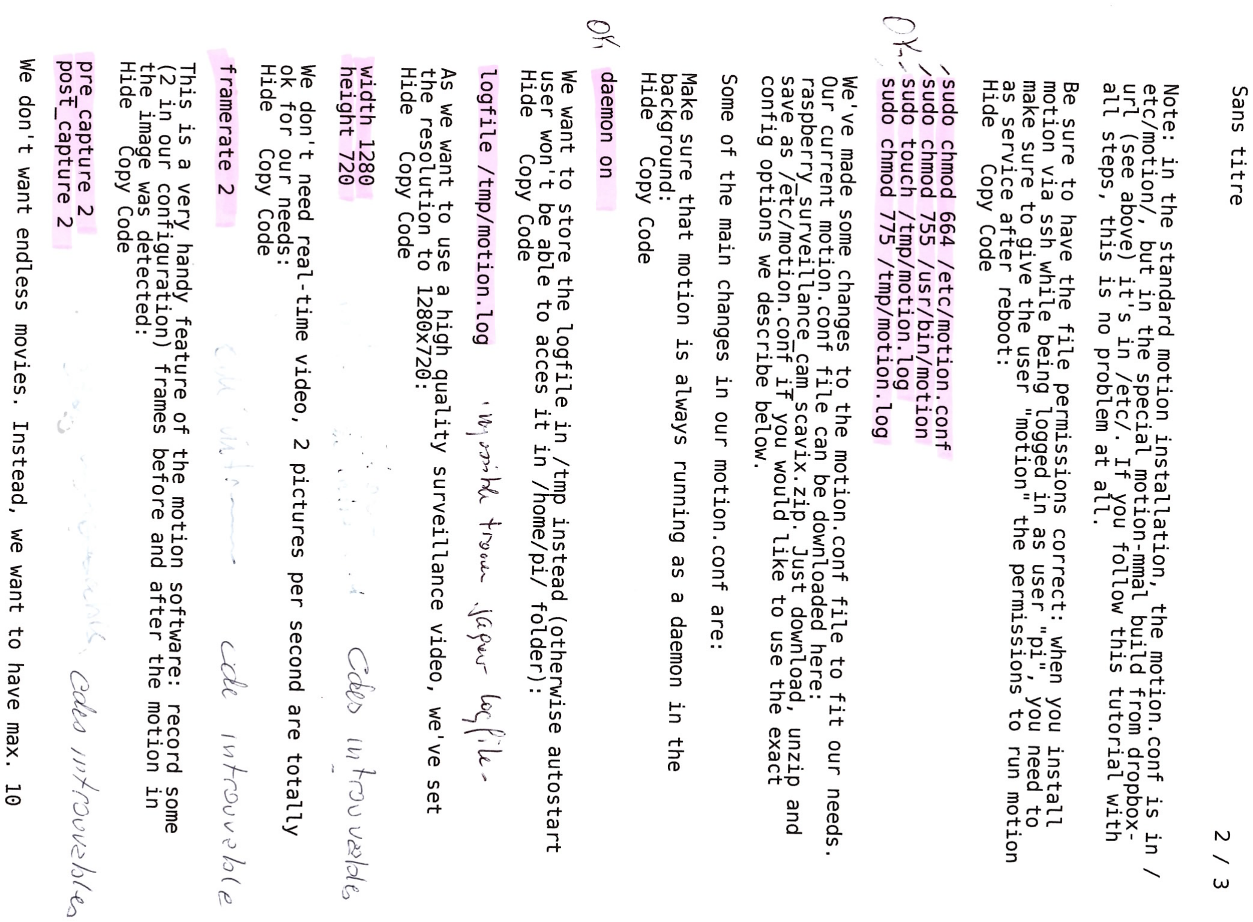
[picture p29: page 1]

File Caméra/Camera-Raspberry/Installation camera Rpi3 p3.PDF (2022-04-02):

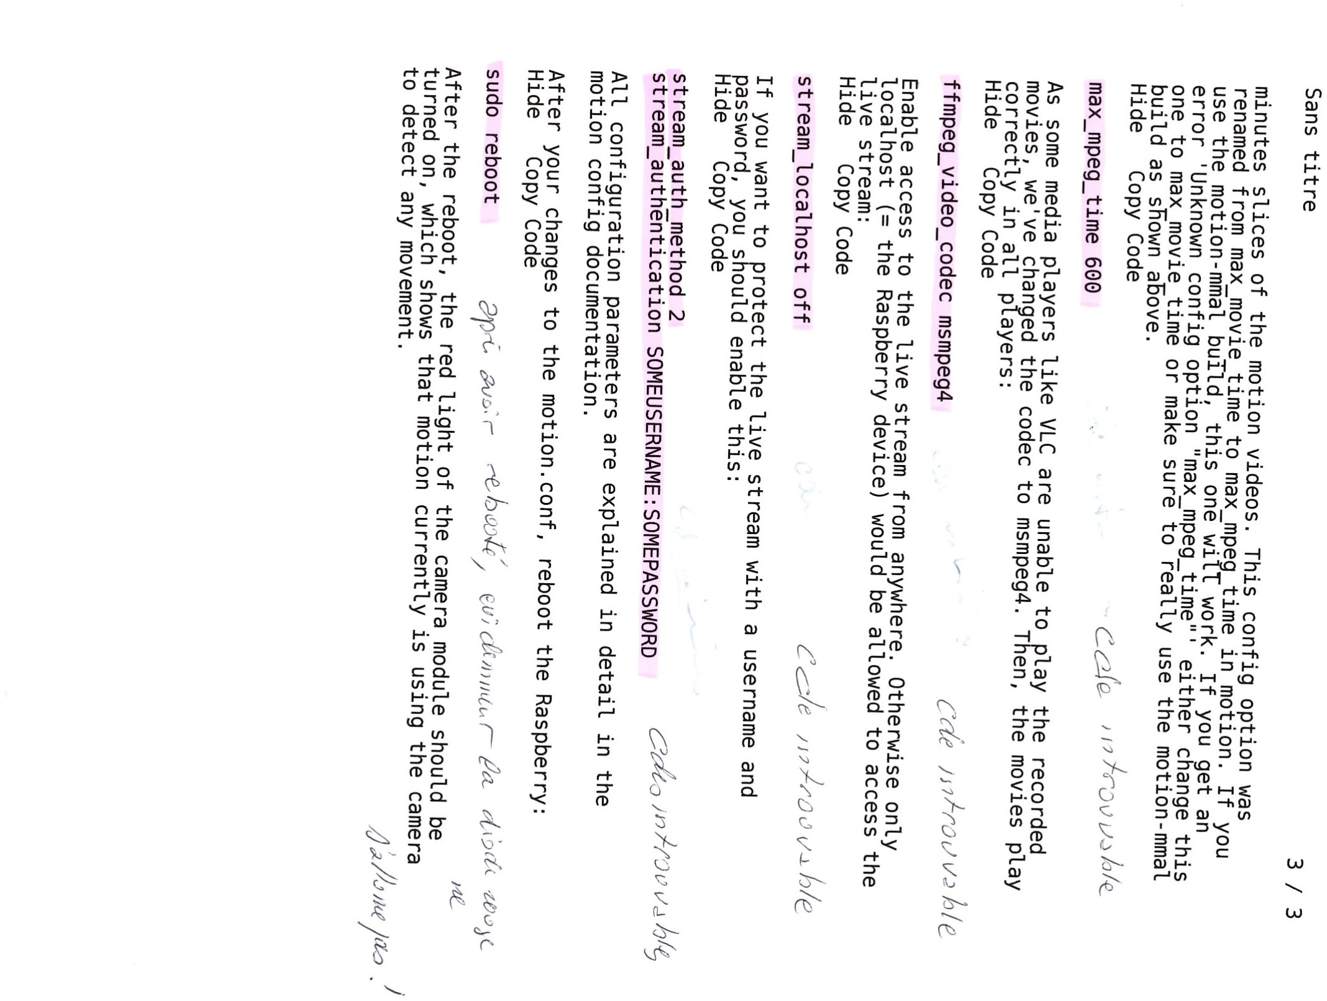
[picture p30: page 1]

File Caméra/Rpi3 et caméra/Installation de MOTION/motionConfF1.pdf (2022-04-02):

MOTION.CONF version francaise

Avant de lancer motion, vous devez :

1) taper en ligne de commande (à chaque démarrage du Rpi):
sudo modprobe bcm2835 -v4l2
Cette commande indique d'utiliser le module videoforlinux du processeur du Rpi
Il sera possible de l'automatiser plus tard éventuellement
2) Paramétrer motion (a faire au départ et à chaque fois que vous désirez changer quelque chose:
Vous trouverez ce fichier de configuration dans :
etc/motion/motion.conf
Pour l'éditer :
cd /etc/motion
sudo nano motion.conf
faire les modifs et le sauvegarder

Voici ce fichier de paramétrage ,traduit en français, pour une meilleure compréhension J'ai surligné les options importantes pour un meilleur repérage
en esperant n'avoir rien oublié:
3) une fois cela fait , vous avez juste à taper en ligne de commande : motion
pour lancer l'application

# Renommez ce fichier d'exemple de distribution sur motion.conf

# Ce fichier de configuration a été généré par motion 4.0.1

# Daemon

# Démarrer en mode démon (arrière-plan) et libérer le terminal (par défaut: désactivé)

daemon off

# Fichier pour stocker l'ID de processus, également appelé fichier pid. (Par défaut: non défini) Process_id_file /var/run/motion/motion.pid

# Mode de configuration de base

# Démarrer en Setup-Mode, démon désactivé. (Par défaut: désactivé)

setup_mode off

# Utiliser un fichier pour enregistrer des messages journaux, si ce n'est pas défini stderr et syslog sont utilisés. ($: Non défini)

;logfile /tmp/motion.log

# Niveau des messages de journal [1..9] (EMG, ALR, CRT, ERR, WRN, NTC, INF, DBG, ALL). (defaut: 6 / NTC)

Log_level 6

# Filtre pour consigner les messages par type (COR, STR, ENC, NET, DBL, EVT, TRK, VID, ALL). (Par défaut: ALL)

log_type all
# Options du périphérique de capture ################################################## ##########

# Videodevice à utiliser pour la capture (par défaut / dev / video0)

# Pour FreeBSD par défaut est / dev / bktr0

Videodevice / dev / video0

# V4l2_palette permet de choisir une palette préférable à utiliser par le mouvement

# À choisir dans ceux pris en charge par votre vidéodevice. (Valeur par défaut: 17)

# Par exemple. Si votre vidéodevice prend en charge à la fois V4L2_PIX_FMT_SBGGR8 et

# V4L2_PIX_FMT_MJPEG alors le mouvement utilisera par défaut V4L2_PIX_FMT_MJPEG. # La définition de v4l2_palette sur 2 force le mouvement à utiliser V4L2_PIX_FMT_SBGGR8 # à la place.

#valeurs :

# V4L2_PIX_FMT_SN9C10X : 0 'S910'

# V4L2_PIX_FMT_SBGGR16 : 1 'BYR2' # V4L2_PIX_FMT_SBGGR8 : 2 'BA81' # V4L2_PIX_FMT_SPCA561 : 3 'S561' # V4L2_PIX_FMT_SGBRG8 : 4 'GBRG' # V4L2_PIX_FMT_SGRBG8 : 5 'GRBG' # V4L2_PIX_FMT_PAC207 : 6 'P207' # V4L2_PIX_FMT_PJPG : 7 'PJPG'

# V4L2_PIX_FMT_MJPEG : 8 'MJPEG' # V4L2_PIX_FMT_JPEG : 9 'JPEG' # V4L2_PIX_FMT_RGB24 : 10 'RGB3' # V4L2_PIX_FMT_SPCA501 : 11 'S501' # V4L2_PIX_FMT_SPCA505 : 12 'S505' # V4L2_PIX_FMT_SPCA508 : 13 'S508' # V4L2_PIX_FMT_UYVY : 14 'UYVY' # V4L2_PIX_FMT_YUYV : 15 'YUYV' # V4L2_PIX_FMT_YUV422P : 16 '422P' # V4L2_PIX_FMT_YUV420 : 17 'YU12'

v4l2_palette 17

# Périphérique de syntonisation à utiliser pour la capture en utilisant le tuner comme source (par défaut / dev / tuner0)

# Ceci est seulement utilisé pour FreeBSD. Laisser commenté pour Linux

; Tunerdevice / dev / tuner0

# L'entrée vidéo à utiliser (par défaut: -1)

# Doit normalement être réglé sur 0 ou 1 pour les cartes vidéo / TV et -1 pour les caméras USB # Définissez à 0 pour uvideo (4) sur OpenBSD

Entrée -1

# La norme vidéo à utiliser (uniquement pour les cartes de capture vidéo et de tuner TV)

# Valeurs: 0 (PAL), 1 (NTSC), 2 (SECAM), 3 (PAL NC pas de couleur). Par défaut: 0 (PAL) Norme 0

# La fréquence de réglage du tuner (kHz) (uniquement pour les cartes tuner TV) (par défaut: 0) Fréquence 0

# Remplace la fréquence de la ligne d'alimentation de la webcam. (Normalement pas nécessaire) # Valeurs:

# -1: Ne modifiez pas le réglage du périphérique

# Définissez à 0 pour uvideo (4) sur OpenBSD

Entrée -1

# La norme vidéo à utiliser (uniquement pour les cartes de capture vidéo et de tuner TV)

# Valeurs: 0 (PAL), 1 (NTSC), 2 (SECAM), 3 (PAL NC pas de couleur). Par défaut: 0 (PAL) Norme 0

# La fréquence de réglage du tuner (kHz) (uniquement pour les cartes tuner TV) (par défaut: 0) Fréquence 0

# Remplace la fréquence de la ligne d'alimentation de la webcam. (Normalement pas nécessaire) # Valeurs:

# -1: Ne modifiez pas le réglage du périphérique

# 0: Fréquence de la ligne de puissance désactivée

# 1: 50hz

# 2: 60hz

# 3: Auto

Power_line_frequency -1

# Faire pivoter l'image pour ce nombre de degrés. La rotation affecte toutes les images enregistrées # Ainsi que des films. Valeurs valides: 0 (par défaut = pas de rotation), 90, 180 et 270.

Tourner 0

# Largeur de l'image (pixels). Plage valide: Selon la caméra, par défaut: 352

Largeur 320

# Hauteur de l'image (pixels). Plage valide: Selon la caméra, par défaut: 288 Hauteur 240

# Nombre maximum d'images à capturer par seconde.

# Plage valide: 2-100. Par défaut: 100 (presque aucune limite).

Framerate 20

# Durée minimale en secondes entre la prise de vues de l'appareil photo.

# Par défaut: 0 = désactivé - le taux de capture est donné par la vitesse d'image de l'appareil photo. # Cette option est utilisée lorsque vous voulez capturer des images à un taux inférieur à 2 par seconde

Minimum_frame_time 0

# URL à utiliser si vous utilisez une caméra réseau, la taille sera automatiquement détectée (incl http:// ftp://mjpg:// rtsp:// mjpeg:// ou fichier:///)

# Doit être une URL qui renvoie des images jpeg simples ou un flux mjpeg brut. Une barre oblique peut être nécessaire pour certaines caméras.

# Par défaut: Non défini

; netcam_url value

# Nom d'utilisateur et mot de passe pour la caméra réseau (uniquement si nécessaire). Par défaut: non defini

# La syntaxe est user: password

; netcam_userpass value

# Le réglage de keep-alive de la prise réseau, devrait améliorer les performances sur les caméras réseau compatible

# Off: L'implémentation historique utilisant HTTP / 1.0, fermant le socket après chaque requête http # Force: Utiliser les requêtes HTTP / 1.0 avec l'en-tête keep alive pour réutiliser la même connexion # On: Utilisez les requêtes HTTP / 1.1 qui prennent en charge le maintien en vie par défaut.

# Par défaut: off

netcam_keepalive off

# URL à utiliser pour un serveur proxy netcam, si nécessaire, p. Ex. "Http: // myproxy".

# Si un numéro de port autre que 80 est nécessaire, utilisez "http: // myproxy: 1234".

# Par défaut: non défini

; netcam_proxy value

# Définir des contrôles jpeg moins stricts pour les caméras réseau avec un micrologiciel pauvre / buggé.

# Par défaut: off

Netcam_tolerant_check off

# La connexion RTSP utilise TCP pour communiquer avec l'appareil photo. Peut empêcher la corruption de l'image

# Par défaut: on

Rtsp_uses_tcp on

# Nom de la caméra à utiliser si vous utilisez une caméra accessible via OpenMax / MMAL # Par défaut: Non défini

; Mmalcam_name vc.ril.camera

# Paramètres de contrôle de la caméra (voir la documentation de l'outil raspivid / raspistill) # Par défaut: Non défini

# Par défaut: Non défini

; Mmalcam_control_params -hf

# Permet au mouvement de régler la luminosité d'un périphérique vidéo (par défaut: désactivé). # La fonction auto_brightness utilise l'option de luminosité comme valeur cible.

# Si la luminosité est nulle auto_brightness s'ajustera à la valeur de luminosité moyenne $

# Seulement recommandé pour les caméras sans luminosité automatique

Auto_brightness off

# Définit la luminosité initiale d'un périphérique vidéo.

# Si auto_brightness est activé, cette valeur définit le niveau de luminosité moyen # Auquel Motion va essayer de s'adapter.

# Plage valide 0-255, défaut 0 = désactivé

brightness 0

# Définit le contraste d'un périphérique vidéo. # Plage valide 0-255, défaut 0 = désactivé Contrast 0

# Définir la saturation d'un périphérique vidéo.

# Plage valide 0-255, défaut 0 = désactivé

Saturation 0

# Définir la teinte d'un périphérique vidéo (fonction NTSC).

# Plage valide 0-255, défaut 0 = désactivé

hue 0

################################################## ########## # Round Robin (plusieurs entrées sur le même nom de périphérique vidéo) ################################################## ##########

# Nombre d'images à capturer dans chaque étape de roundrobin (par défaut: 1) Roundrobin_frames 1

# Nombre d'images à sauter avant chaque étape roundrobin (par défaut: 1) roundrobin_skip 1

# Essayez de filtrer le bruit généré par round robin (par défaut: off) switchfilter off

################################################## ########## # Paramètres de détection de mouvement: ################################################## ##########

# Seuil pour le nombre de pixels modifiés dans une image qui

# Déclenche la détection de mouvement (par défaut: 1500) 0 = streaming continu #mais motion est tres mauvais pour du streaming ,vous pourrez tester

threshold 1500

# Régler automatiquement le seuil si possible (par défaut: désactivé) threshold_tune off

# Seuil de bruit pour la détection de mouvement (par défaut: 32) noise_level 32

# Réglage automatique du seuil de bruit (par défaut: activé)

noise_tune on

# Dépochez l'image de mouvement en utilisant (e)rode ou (d)ilate ou (l) abel (Défaut: non défini) # La valeur recommandée est EedDl. Toute combinaison (et nombre de) de E, e, d et D est valide

# (L) abeling doit être utilisé une seule fois et le « l » doit être la derniere lettre

# commenter pour désactiver

despeckle_filter EedDl

# Détecter le mouvement dans les zones prédéfinies (1 - 9). Les zones sont numérotées comme ça: 1 2 3

# Un script (on_area_detected) est démarré immédiatement lorsque le mouvement est 4 5 6

# Détecté dans l'une des zones données, mais seulement une fois pendant un événement. 7 8 9

# Une ou plusieurs zones peuvent être spécifiées avec cette option. Attention: Cette option

# NE limite PAS la détection à ces zones! (Par défaut: non défini)

; Area_detect value

# Fichier PGM à utiliser comme masque de sensibilité.

# Chemin d 'accès complet à. (Par défaut: non défini)

; Valeur masque_fichier

# Créer dynamiquement un fichier de masque pendant l'opération (par défaut: 0)

# Régler la vitesse des changements de masque de 0 (arrêt) à 10 (rapide) Smart_mask_speed 0

# Ignorer les changements brusques d'intensité lumineuse dus en pourcentage de l'image # Zone qui a changé d'intensité. Plage valide: 0 - 100, par défaut: 0 = désactivé

lightswitch 0

# Les cadres doivent contenir au moins le nombre spécifié d'images

# Dans une rangée avant qu'ils ne soient détectés comme mouvement vrai. À la valeur par défaut 1, #tous les mouvements sont détectés. Plage valide: 1 à milliers, recommandé 1-5 minimum_motion_frames 1

# Spécifie le nombre d'images pré-capturées (tamponnées) ,avant que le mouvement

# soit détecté ,qui sera émis lors de la détection de mouvement.

# Plage recommandée: 0 à 5 (par défaut: 0)

# Ne pas utiliser de grandes valeurs! Les valeurs élevées amèneront Motion à ignorer les images vidéo et

# à provoquer des films lissés. Pour lisser les films, utilisez plutôt les valeurs de post_capture. Pre_capture 0

# Nombre d'images à capturer après que le mouvement ne soit plus détecté (par défaut: 0) Post_capture 0

# Event Gap est la seconde absence de détection de mouvement qui déclenche la fin d'un événement.

# Un événement est défini comme une série d'images animées prises dans un court laps de temps. # La valeur recommandée est 60 secondes (par défaut). La valeur -1 est autorisée et désactive les # Événements provoquant l'écriture de tous les mouvements dans un fichier vidéo unique et pas de pré-capture.

# Si cette valeur est définie sur 0, le mouvement est en mode sans épaulement. Les films n'ont plus de lacunes. Un evenement

# Se termine juste après que plus aucun mouvement n'est détecté et que post_capture est terminé.

event_gap 60

# Longueur maximale en secondes d'un film

# Lorsque la valeur est dépassée, un nouveau fichier de film est créé. (Par défaut: 0 = infini) max_movie_time 0

# Sauvegardez toujours les images même s'il n'y a pas de mouvement (par défaut: désactivé) emulate_motion off

# Fichier d'image

# Sortie des images 'normales' lorsque le mouvement est détecté (par défaut: activé)

# Valeurs valides: on, off, first, best, center

# Lorsqu'il est réglé sur 'first', seule la première image d'un événement est enregistrée.

# L'image avec la plupart des mouvements d'un événement est enregistrée lorsqu'elle est réglée sur "meilleur".

# L'image avec le mouvement le plus proche du centre de l'image est sauvegardée lorsqu'elle est réglée sur "centre".

# Peut être utilisé comme prévisualisation pour le film correspondant.

output_pictures off

# Sortie des images avec seulement les pixels déplacement de l'objet (images fantômes) (par défaut: désactivé)

output_debug_pictures off

# La qualité (en pourcentage) à utiliser par la compression jpeg (par défaut: 75)

quality 75

# Type d'images de sortie

# Valeurs valides: jpeg, ppm (par défaut: jpeg)

picture_type jpeg

################################################## ########## # FFMPEG options liées

# Sortie fichier film (films), et désentrelacement de l'entrée vidéo

# Les options movie_filename et timelapse_filename sont également utilisées # Par la fonctionnalité ffmpeg ################################################## ##########

# Utilisez ffmpeg pour encoder des films en temps réel (par défaut: désactivé) ffmpeg_output_movies on

# Utilisez ffmpeg pour faire des films avec seulement les pixels en mouvement # Objet (images fantômes) (par défaut: désactivé)

ffmpeg_output_debug_movies off

# Utilisez ffmpeg pour encoder un film timelapse

# Valeur par défaut 0 = off - else Enregistrer la trame chaque Nième seconde

ffmpeg_timelapse 0

# Le mode de survol du fichier de la vidéo timelapse

# Valeurs valides: horaire, quotidien (par défaut), hebdomadaire-hebdomadaire, hebdomadaire-lundi, mensuel, manuel

ffmpeg_timelapse_mode daily

# Bitrate à utiliser par l'encodeur ffmpeg (par défaut: 400000)

# Cette option est ignorée si ffmpeg_variable_bitrate n'est pas 0 (désactivé) ffmpeg_bps 400000

# Active et définit le débit binaire variable pour l'encodeur ffmpeg.

# Ffmpeg_bps est ignoré si le débit binaire variable est activé.

# Valeurs valides: 0 (par défaut) = débit fixe défini par ffmpeg_bps, # Ou la plage 1 - 100 où 1 signifie pire qualité et 100 est le meilleur. ffmpeg_variable_bitrate 0

# Codec utilisé par ffmpeg pour la compression vidéo.

# Timelapse vidéos ont deux options.

# Mpg - Crée un fichier mpg avec encodage mpeg-2.

# Si le mouvement est arrêté et redémarré, de nouvelles images seront ajoutées # À tout fichier précédemment créé avec le nom indiqué pour timelapse.

# Mpeg4 - Crée un fichier avi avec l'encodage par défaut.

# Si le mouvement est arrêté et redémarré, de nouvelles photos créeront un

# Nouveau fichier avec le nom indiqué pour timelapse.

# Les formats supportés sont:

# Mpeg4 ou msmpeg4 - vous donne des fichiers avec extension .avi

# Msmpeg4 est recommandé pour une utilisation avec Windows Media Player, car

# Il ne nécessite aucune installation de codec sur le client Windows.

# swf - vous donne un film flash avec extension .swf

# flv - vous donne une vidéo flash avec l'extension .flv

# ffv1 - Codec vidéo FF 1 pour le codage sans perte

# mov - QuickTime

# mp4 - MPEG-4 Part 14 H264 encodage

# mkv - Codage Matroska H264

# hevc - H.265 / HEVC (Codage vidéo haute efficacité)

ffmpeg_video_codec mpeg4

# Lors de la création de vidéos, les images doivent-elles être dupliquées pour # Pour suivre les images demandées par seconde

# (Par défaut: vrai)

ffmpeg_duplicate_frames true

################################################## ########## # Fenêtre SDL

# Nombre de threads de mouvement à afficher dans la fenêtre SDL (par défaut: 0 = désactivé) #sdl_threadnr 0

# Capteur externe de canal vers vidéo

# Remplacement de l'encodeur builder FFMPEG pour ffmpeg_output_movies uniquement. # Les options movie_filename et timelapse_filename sont également utilisées

# Par la fonctionnalité ffmpeg

# Booleen pour activer ou désactiver le canal externe (par défaut: désactivé) use_extpipe off

# Programme externe (chemin complet et opte) pour canaliser la vidéo brute vers

# Généralement, utilisez '-' pour STDIN ...

;extpipe mencoder -demuxer rawvideo -rawvideo w=%w:h=%h:i420 -ovc x264 -x264encopts bframes=4:frameref=1:subq=1:scenecut=-1:nob_adapt:threads=1:keyint=1000:8x8dct:vbv_bufsize=4000:crf=24:partitions=i8x8,i4x4:vbv_ma xrate=800:no-chroma-me -vf denoise3d=16:12:48:4,pp=lb -of avi -o %f.avi - -fps %fps
;extpipe x264 - --input-res %wx%h --fps %fps --bitrate 2000 --preset ultrafast --quiet -o %f.mp4 ;extpipe mencoder -demuxer rawvideo -rawvideo w=%w:h=%h:fps=%fps -ovc x264 -x264encopts preset=ultrafast -of lavf -o %f.mp4 - -fps %fps
;extpipe ffmpeg -y -f rawvideo -pix_fmt yuv420p -video_size %wx%h -framerate %fps -i pipe 0 : -vcodec libx264 -preset ultrafast -f mp4 %f.mp4
# Snapshots (sortie de fichier périodique traditionnelle de webcam) ################################################## ##########

# Effectuer instantané automatique toutes les N secondes (par défaut: 0 = désactivé)

snapshot_interval 0

################################################## ########## # Afficheur de texte

#% Y = année,% m = mois,% d = date,

% H = heure,% M = minute,% S = seconde,% T = HH: MM: SS,
#% V = événement,% q = numéro d'image,% t = numéro d'identification de la caméra, #% D = pixels modifiés,% N = niveau de bruit, \ n = nouvelle ligne,

#% I et% J = largeur et hauteur de la zone de mouvement,

#% K et% L = coordonnées X et Y du centre de mouvement

#% C = valeur définie par text_event - ne pas utiliser avec text_event! # Vous pouvez placer des guillemets autour du texte pour

# les espaces principaux

# Localiser et dessiner une boîte autour de l'objet en mouvement.

# Valeurs valides: on, off, preview (par défaut: off)

# Set to 'preview' ne fera que dessiner une boîte dans les images preview_shot. locate_motion_mode off

# Définissez l'aspect et le style de la zone de localisation si cette option est activée. # Valeurs valides: box, redbox, cross, redcross (par défaut: box)

# Set to 'box' va dessiner la boîte traditionnelle.

# Set to 'redbox' va dessiner une boîte rouge.

# Set to 'cross' va dessiner une petite croix pour marquer le centre.

# Set to 'redcross' va dessiner une petite croix rouge pour marquer le centre. locate_motion_style box

# Dessine l'horodatage en utilisant les mêmes options que la fonction C strftime (3)

# Valeur par défaut:% Y-% m-% d \ n% T = date au format ISO et heure en 24 heures

# Le texte est placé dans le coin inférieur droit

text_right %Y-%m-%d\n%T-%q

# Dessine un texte défini par l'utilisateur sur les images en utilisant les mêmes options que la fonction C strftime (3)

# Par défaut: Non défini = pas de texte

# Le texte est placé dans le coin inférieur gauche

; text_left CAMERA %t

# Dessinez le nombre de pixels modifiés sur les images (par défaut: désactivé)

# Normalement, le réglage est désactivé, sauf lorsque vous configurez et ajustez les paramètres de déplacement

# Le texte est placé dans le coin supérieur droit

text_changes off

# Cette option définit la valeur du spécificateur de conversion d'événement spécial% C

# Vous pouvez utiliser n'importe quel spécificateur de conversion dans cette option à l'exception de % C. Date et l'heure

# Valeurs sont à partir de l'horodatage de la première image dans l'événement en cours.

# Valeur par défaut:% Y% m% d% H% M% S

# L'idée est que% C peut être utilisé pour filenames et text_left / right pour créer

# Un identifiant unique pour chaque événement.

text_event %Y%m%d%H%M%S

# Dessine des caractères à deux fois la taille normale sur les images. (Par défaut: désactivé) text_double off

# Texte à inclure dans un commentaire JPEG EXIF

# Peut être n'importe quel texte, y compris les spécificateurs de conversion. # L'horodatage EXIF est inclus indépendamment de ce texte.

;exif_text %i%J/%K%L

################################################## ########## # Répertoires cibles et noms de fichiers pour les images et les films

# Pour les options snapshot_, picture_, movie_ et timelapse_filename

# Vous pouvez utiliser des spécificateurs de conversion

#% Y = année,% m = mois,% d = date,

#% H = heure,% M = minute,% S = seconde,

#% V = événement,% q = numéro d'image,% t = numéro d'identification de la caméra, #% D = pixels modifiés,% N = niveau de bruit,

#% I et% J = largeur et hauteur de la zone de mouvement,

#% K et% L = coordonnées X et Y du centre de mouvement

#% C = valeur définie par text_event

# La chaîne ronde des guillemets est autorisée.

# Répertoire cible des images et des films

# Recommandé pour utiliser le chemin absolu. (Par défaut: répertoire de travail courant) #target_dir / tmp / motion

# Chemin du fichier pour les instantanés (jpeg ou ppm) par rapport à target_dir

# Valeur par défaut:% v-% Y% m% d% H% M% S-snapshot

# La valeur par défaut est équivalente à l'ancienne option legacy oldlayout

# Pour le mode compatible avec Motion 3.0, choisissez:% Y /% m /% d /% H /% M /% S-snapshot # L'extension de fichier .jpg ou .ppm est automatiquement ajoutée, donc n'incluez pas cela.

# Note: Un lien symbolique appelé lastsnap.jpg créé dans le target_dir sera toujours

# Pointer vers le dernier instantané, à moins que snapshot_filename soit exactement 'lastsnap'

snapshot_filename %v-%Y%m%d%H%M%S-snapshot

# Chemin du fichier pour les images déclenchées par mouvement (jpeg ou ppm) par rapport à target_dir

# Valeur par défaut:% v-% Y% m% d% H% M% S-% q

# La valeur par défaut est équivalente à l'ancienne option legacy oldlayout

# Pour le mode compatible Motion 3.0, choisissez:% Y /% m /% d /% H /% M /% S-% q

# L'extension de fichier .jpg ou .ppm est automatiquement ajoutée, donc n'incluez pas cette

# Définir la prévisualisation avec la fonction de prévisualisation optimale permet une nomination spéciale

# Convention pour les plans d'aperçu. Voir le guide de la motion pour plus de détails picture_filename %v-%Y%m%d%H%M%S-%q

# Chemin du fichier pour les films ffmpeg déclenchés par le mouvement (films) par rapport à target_dir

# Valeur par défaut:% v-% Y% m% d% H% M% S

# Les extensions de fichier (.mpg .avi) sont automatiquement ajoutées, ne les incluez donc pas movie_filename %v-%Y%m%d%H%M%S

# Chemin du fichier pour les films temporels par rapport à la cible

# Valeur par défaut:% Y% m% d-timelapse

# Les extensions de fichier (.mpg .avi) sont automatiquement ajoutées, ne les incluez donc pas

movie_filename %v-%Y%m%d%H%M%S

# Chemin du fichier pour les films temporels par rapport à la cible

# Valeur par défaut:% Y% m% d-timelapse

# Les extensions de fichier (.mpg .avi) sont automatiquement ajoutées, ne les incluez donc pas timelapse_filename %Y%m%d-timelapse

################################################## ########## # Options de réseau mondial ################################################## ########## # Activer IPv6 (par défaut: désactivé)

Ipv6_enabled off

################################################## ########## # Serveur de flux en direct

# pour réseau local

# Le serveur mini-http écoute ce port pour les requêtes (par défaut: 0 = désactivé) stream_port 8090

stream_quality 50

# Sortie des images à 1 fps lorsqu'aucun mouvement n'est détecté et augmente

# Taux donné par stream_maxrate lorsque le mouvement est détecté (par défaut: off) # on pour diffusion sur reseau local

stream_motion off

# Framerate maximum pour les flux (par défaut: 1)

stream_maxrate 20

# Limiter les connexions de flux à localhost uniquement (par défaut: activé) #localhost = le Rpi lui même donc à désactiver (off) pour affichage distant stream_localhost on

# Limite le nombre d'images par connexion (par défaut: 0 = illimité)

# Le nombre peut être défini en multipliant le débit réel par le nombre désiré de secondes

# Taux de flux réel est le plus petit des framerate nombre et stream_maxrate stream_limit 0

# Définir la méthode d'authentification (par défaut: 0)

# 0 = désactivé

# 1 = Authentification de base

# 2 = Digest MD5 (l'authentification plus sûre)

stream_auth_method 0

# Authentification pour le flux. Syntaxe nom d'utilisateur: mot de passe # Par défaut: non défini (Désactivé)

; Nom_utilisateur stream_authentication: mot de passe

# Pourcentage d'échelle de l'image de flux pour la prévisualisation

# Par défaut: 25

; stream_preview_scale 25

# Avez l'image d'aperçu de flux commencer sur une nouvelle ligne

# Par défaut: non

; Stream_preview_newline non

################################################## ########## # Contrôle basé sur HTTP

################################################## ########## # sert pour l'accès par internet

# Port TCP / IP pour le serveur HTTP à écouter (par défaut: 0 = désactivé) webcontrol_port 8080

# Restriction des connexions de contrôle à localhost uniquement (par défaut: activé) webcontrol_localhost on

# Sortie pour le serveur http, sélectionnez désactiver pour choisir le texte brut simple (par défaut: activé)

webcontrol_html_output on

# Authentification pour le contrôle basé sur http. Syntaxe nom d'utilisateur: mot de passe # Par défaut: non défini (Désactivé)

; Nom d'utilisateur de webcontrol_authentication: mot de passe
# Suivi (Pan / Tilt)

# Type de tracker (0 = none (par défaut), 1 = stepper, 2 = iomojo, 3 = pwc, 4 = générique, 5 = uvcvideo, $

# Le type générique permet la définition du centre de mouvement et de la taille du mouvement

# Être utilisé avec les spécificateurs de conversion pour des options comme on_motion_detected track_type 0

track_auto off

# Port série du moteur (par défaut: aucun)

; track_port / dev / ttyS0

# Numéro du moteur pour l'axe des x (valeur par défaut: 0) ; track_motorx 0

# Réglage motorx reverse (par défaut: 0)

; track_motorx_reverse 0

# Numéro du moteur pour l'axe des y (par défaut: 0) ; track_motory 1

# Réglage de l'inversion motrice (par défaut: 0)

; track_motory_reverse 0

# Valeur maximale sur l'axe des x (valeur par défaut: 0) ; track_maxx 200

# Valeur minimale sur l'axe des x (valeur par défaut: 0) ; track_minx 50

# Valeur maximale sur l'axe des y (par défaut: 0)

; track_maxy 200

# Valeur minimale sur l'axe des y (par défaut: 0)

; track_miny 50

# Valeur centrale sur l'axe des x (valeur par défaut: 0) ; track_homex 128

# Valeur centrale sur l'axe des y (valeur par défaut: 0) ; track_homey 128

# ID d'une caméra iomojo si utilisée (par défaut: 0) track_iomojo_id 0

# Angle en degrés de la caméra se déplace par pas sur l'axe X

# Avec auto-track (par défaut: 10)

# Actuellement utilisé uniquement avec les caméras de type pwc

track_step_angle_x 10

# Angle en degrés de la caméra se déplace par pas sur l'axe des Y # Avec auto-track (par défaut: 10)

# Actuellement utilisé uniquement avec les caméras de type pwc track_step_angle_y 10

# Délai d'attente après suivi du mouvement en tant que nombre

Nombre de cadres photo (par défaut: 10)
track_move_wait 10

# Vitesse pour régler le moteur sur (option moteur pas à pas) (valeur par défaut: 255) track_speed 255

# Nombre de pas à faire (option moteur pas à pas) (par défaut: 40)

track_stepsize 40

# Commandes externes, mises en garde et enregistrement:

# Vous pouvez utiliser des spécificateurs de conversion pour les commandes on_xxxx #% Y = année,% m = mois,% d = date,

#% H = heure,% M = minute,% S = seconde,

#% v = événement,% q = numéro d'image,% t = numéro d'identification de la caméra, #% D = pixels modifiés,% N = niveau de bruit,

#% i et% J = largeur et hauteur de la zone de mouvement,

#% K et% L = coordonnées X et Y du centre de mouvement

#% C = valeur définie par text_event

#% f = nom de fichier avec le chemin complet

#% n = nombre indiquant le type de fichier

# Les deux% f et% n ne sont définis que pour on_picture_save,

# On_movie_start et on_movie_end

# La chaîne ronde des guillemets est autorisée. ################################################## ##########

# Ne pas émettre de bip sonore lors de la détection de mouvement (par défaut: activé) # Note: Le mouvement ne sonne jamais lorsque vous exécutez en mode daemon.

Quiet on

# Commande à exécuter lorsqu'un événement démarre. (Par défaut: aucun)

# Un événement commence au premier mouvement détecté après une période sans mouvement défini par event_gap

; on_event_start value

# Commande à exécuter lorsqu'un événement se termine après une période sans mouvement # (Par défaut: aucun). La période sans mouvement est définie par l'option event_gap.

; on_event_end value

# Commande à exécuter lorsqu'une image (.ppm | .jpg) est enregistrée (par défaut: aucune)

# Pour donner le nom de fichier en tant qu'argument à une commande, ajoutez-le avec% f ; on_picture_save value

# Commande à exécuter lorsqu'un cadre de mouvement est détecté (par défaut: aucun)

; On_motion_detected value

# Commande à exécuter lorsque le mouvement dans une zone prédéfinie est détecté

# Vérifiez l'option 'area_detect'. (Par défaut: aucun)

; On_area_detected value
# Commande à exécuter lorsqu'un fichier de film (.mpg | .avi) est créé. (Par défaut: aucun)

# Pour donner le nom de fichier en tant qu'argument à une commande, ajoutez-le avec% f

; on_movie_start value

# Commande à exécuter lorsqu'un fichier de film (.mpg | .avi) est fermé. (Par défaut: aucun)

# Pour donner le nom de fichier en tant qu'argument à une commande, ajoutez-le avec% f ; on_movie_end value

# Commande à exécuter lorsqu'une caméra ne peut pas être ouverte ou si elle est perdue

# REMARQUE: Il ya des situations où le mouvement ne détecte pas une caméra perdue!

# Il dépend du pilote, certains conducteurs ne détectent pas une caméra perdue à tous

# Certains bloquent le thread de mouvement. Certains bloquent même le PC! (Par défaut: aucun)

; on_camera_lost value

################################################## ################### # Options communes pour les fonctionnalités de base de données.

# Les options requièrent que les options de base de données soient également actives.

# Se connecter à la base de données lors de la création d'un fichier image déclenché par mouvement (par défaut: activé)

; sql_log_picture on

# Se connecter à la base de données lors de la création d'un fichier image d'instantané (par défaut: activé)

; sql_log_snapshot on

# Se connecter à la base de données lors de la création d'un fichier vidéo déclenché par mouvement (par défaut: désactivé)

; sql_log_movie off

# Se connecter à la base de données lors de la création d'un fichier de films timelapse (par défaut: désactivé)

; sql_log_timelapse désactivé

# Chaîne de requête SQL envoyée à la base de données

# Utiliser les mêmes spécifications de conversion pour les fonctionnalités de texte # Les spécificateurs de conversion spéciaux supplémentaires sont

#% n = nombre représentant le type_fichier

#% f = nom de fichier avec le chemin complet

# Valeur par défaut:

# Créer des tables:

# Mysql

# CREATE TABLE security (caméra int, nom de fichier char (80) non null, frame int, type_fichier int, ti $ $ nt, time_stamp timestamp (14), event_time_stamp timestamp (14));

# Postgresql

# CREATE TABLE security (caméra int, nom de fichier char (80) pas null, frame int, type_fichier int, ti $ $ nt, time_stamp timestamp sans fuseau horaire, event_time_stamp timestamp sans fuseau horaire);

# Insérer dans les valeurs de sécurité (caméra, nom de fichier, frame, type_fichier, time_stamp, text_event) ('% t $

; sql_query insert into security (caméra, nom de fichier, frame, type_fichier, time_stamp, time_time_s $$ time_stamp) valeurs ('% t', '% f', '% q', '% n', '% Y-% m-% D% T ','% C ')
# Options de base de données

# Type de base de données: mysql, postgresql, sqlite3 (par défaut: non défini) ; Valeur de la base de données

# Base de données à ouvrir une session (par défaut: non défini)

# Pour sqlite3, le chemin d'accès complet et le nom de la base de données.

; database_dbname value

# L'hôte sur lequel se trouve la base de données (par défaut: localhost)

; database_host value

# Nom du compte utilisateur pour

; database_user value

# Mot de passe utilisateur pour la base de données (par défaut: non défini) ; database_password value

# Port sur lequel se trouve la base de données

# Mysql 3306, postgresql 5432 (par défaut: non défini)

; database_port value

# Temps d'attente de base de données en millisecondes pour la base de données verrouillée à # Être déverrouillé avant de retourner la base de données verrouillée erreur (par défaut 0)

; database_busy_timeout 0
# Dispositif de bouclage vidéo (projet vloopback) ################################################## ##########

# Sortie d'images vers un périphérique de bouclage vidéo4linux

# La valeur '-' signifie suivante disponible (par défaut: non définie)

; video_pipe valeur

# Sortie d'images animées vers un périphérique de bouclage vidéo4linux

# La valeur '-' signifie suivante disponible (par défaut: non définie)

; motion_video_pipe valeur
# Fichiers de configuration de la caméra - Un pour chaque caméra.

# Sauf si une seule caméra - Vous avez seulement besoin de ce fichier de configuration. # Si vous avez plus d'une caméra, vous DEVEZ définir une caméra

# Fichier de configuration pour chaque caméra en plus de ce fichier de configuration. ################################################## ############

# Rappelez-vous: si vous avez plus d'une caméra, vous devez en avoir une

# Fichier caméra pour chaque caméra. Par exemple. 2 caméras nécessite 3 fichiers: # Ce fichier motion.conf ET camera1.conf et camera2.conf.

# Ne mettre que les options qui sont uniques à chaque caméra

# Fichiers de configuration de la caméra

; camera /etc/motion/camera1.conf
; camera /etc/motion/camera2.conf

; camera /etc/motion/camera3.conf
; camera /etc/motion/camera4.conf

############################################################## # Camera config directory - One for each camera. ############################################################## #

; camera_dir /etc/motion/conf.d

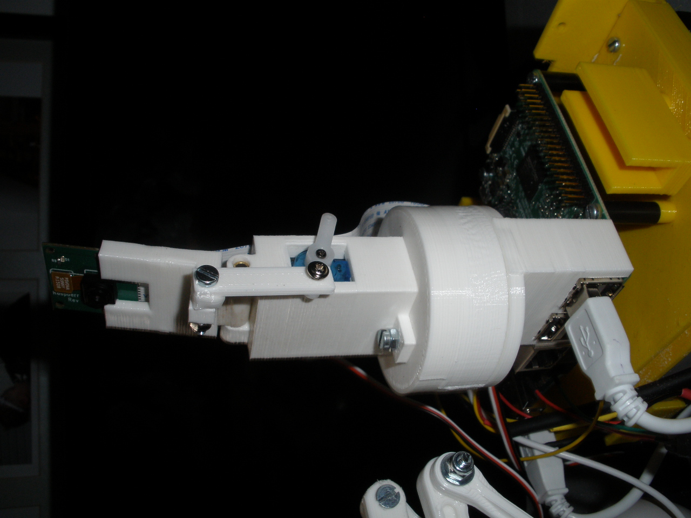
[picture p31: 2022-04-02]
fichiers STL/Pan tilt/Photos pour montage/5- vue générale pan-tilt.JPG

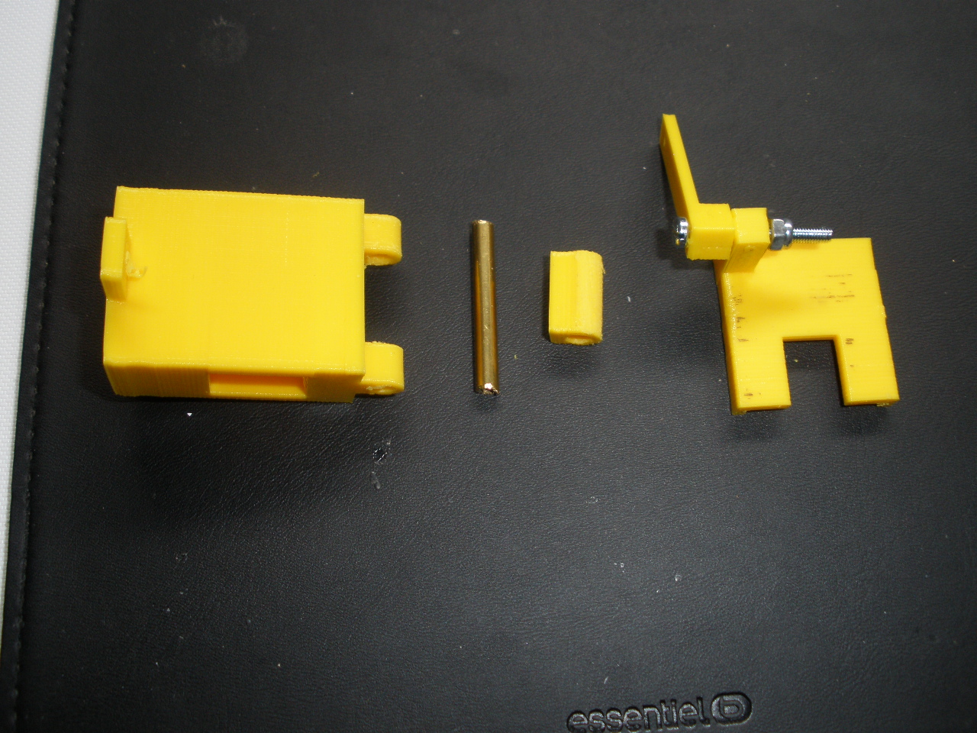
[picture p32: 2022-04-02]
fichiers STL/Pan tilt/Photos pour montage/Photos pour impression/Elements de la partie haute.JPG

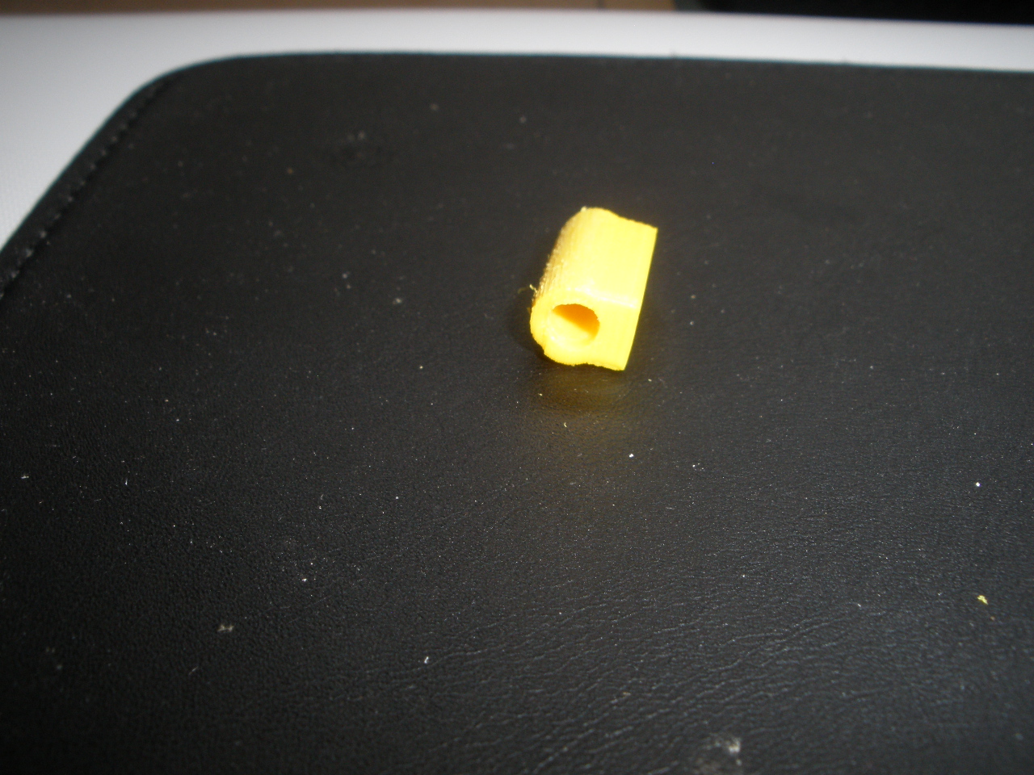
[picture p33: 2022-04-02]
fichiers STL/Pan tilt/Photos pour montage/Photos pour impression/Pivot.JPG

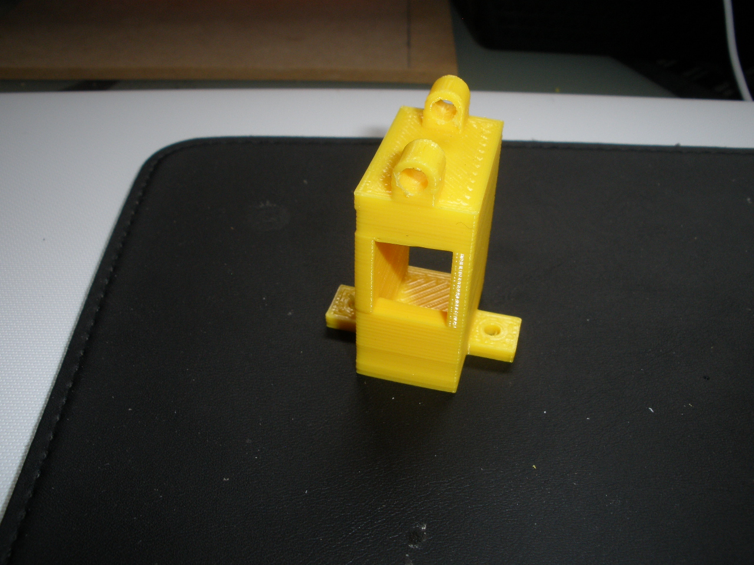
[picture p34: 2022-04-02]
fichiers STL/Pan tilt/Photos pour montage/Cagehaut.JPG

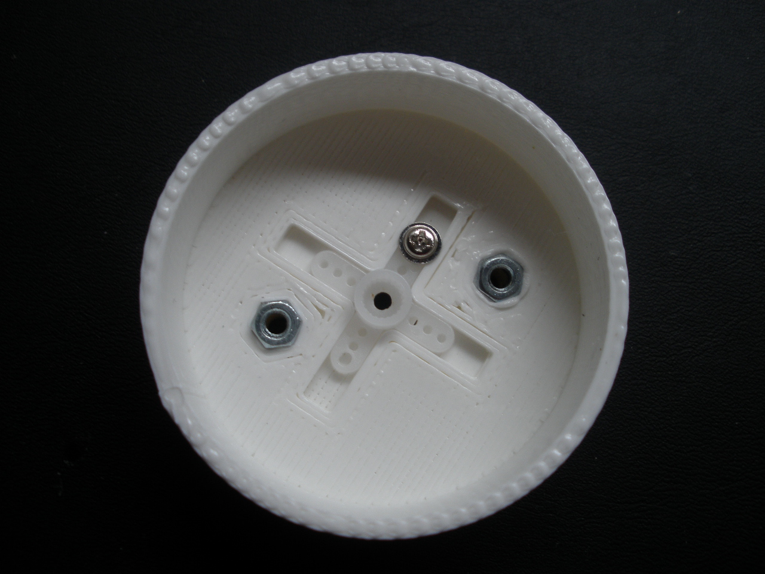
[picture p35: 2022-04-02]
fichiers STL/Pan tilt/Photos pour montage/2- Fixation palonnier servo sur la base tournante.JPG

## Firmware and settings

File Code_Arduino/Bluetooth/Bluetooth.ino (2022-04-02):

#include "UART.h"
#include "HBRIDGE.h"
#include "LED.h"

#include <Servo.h>

#define SENS_1 0
#define SENS_2 1

const byte enable_moteur_droite = 5; //Broche PWM
const byte enable_moteur_gauche = 6; //Broche PWM
const byte sens_moteur_droite = 7; 	
const byte sens_moteur_gauche = 8;

const int SHARP = A0;


int RX_HC = 12;//12
int TX_HC = 10;//10

int position_servo_180 = 90;
int position_servo_120 = 90;

int distance = 0;
int nb_lecture_sharp = 10;


UART hc_05(RX_HC,TX_HC);
HBRIDGE robot(enable_moteur_gauche, sens_moteur_gauche, enable_moteur_droite, sens_moteur_droite);
LED led_verte(9);
LED led_jaune(3);
LED led_defaut(13);

Servo servo_rpi_180;
Servo servo_rpi_120;
//String message_pi;
String message_hc;

byte puissance_moteur = 100;

void setup() {

//robot.debug();
Serial.begin(9600);
hc_05.begin(9600);
led_defaut.on();
led_verte.on(1000);
led_jaune.on();
servo_rpi_180.attach(3);
servo_rpi_120.attach(4);


servo_180(position_servo_120,90,40);
servo_120(position_servo_120,90,40);
}

void loop() {
  
message_hc = hc_05.read();
//message_pi = rpi.read();

 
if(message_hc!="") { 
   //Serial.println(message_hc);
   
   if(message_hc=="a")      {robot.motor_on(SENS_1,puissance_moteur, SENS_1, puissance_moteur);led_jaune.off();}
   else if(message_hc=="r") {robot.motor_on(SENS_2,puissance_moteur, SENS_2, puissance_moteur);
                             led_jaune.on();}
   else if(message_hc=="d") {robot.motor_on(SENS_1,puissance_moteur, SENS_2, puissance_moteur);led_jaune.off();}
   else if(message_hc=="g") {robot.motor_on(SENS_2,puissance_moteur, SENS_1, puissance_moteur);led_jaune.off();}
   else if(message_hc=="s") {robot.motor_off(0,0);led_jaune.off();}
   else if(message_hc=="1") {puissance_moteur=25;}
   else if(message_hc=="2") {puissance_moteur=50;}
   else if(message_hc=="3") {puissance_moteur=75;}
   else if(message_hc=="4") {puissance_moteur=100;}
   else if(message_hc=="5") {puissance_moteur=125;}
   else if(message_hc=="6") {puissance_moteur=150;}
   else if(message_hc=="7") {puissance_moteur=175;}
   else if(message_hc=="8") {puissance_moteur=200;}
   else if(message_hc=="9") {puissance_moteur=225;}
   else if(message_hc=="10"){puissance_moteur=255;}
   
   else if(message_hc=="11")  {servo_180(position_servo_180,20,40);}//servo_180(position_servo_180,20,40);
   else if(message_hc=="12")  {servo_180(position_servo_180,45,40);}
   else if(message_hc=="13")  {servo_180(position_servo_180,90,40);}
   else if(message_hc=="14")  {servo_180(position_servo_180,135,40);;}
   else if(message_hc=="15")  {servo_180(position_servo_180,160,40);}

   else if(message_hc=="20")  {servo_120(position_servo_120,30,40);}
   else if(message_hc=="21")  {servo_120(position_servo_120,60,40);}
   else if(message_hc=="22")  {servo_120(position_servo_120,90,40);}
   else if(message_hc=="23")  {servo_120(position_servo_120,120,40);}
   else if(message_hc=="24")  {servo_120(position_servo_120,140,40);}
   
   else if(message_hc=="c") {led_verte.blink(200,100,8);
                             //rpi.send("connect");
                             led_verte.on();}
   //else if(message_hc=="camera") {rpi.send("camera");}
 
}//fin if 


}//fin loop
//                    90                10
void servo_180(int pos_origine, int pos_expected, int delai_pas) {

   int delta = pos_expected - pos_origine;  //10-90 = -80
   int delta_abs = abs(delta);//80
   int pas = delta/delta_abs;//-1

   for (int i=0; i< delta_abs;i++) {  // défile n positions pour atteindre l'angle final     
         pos_origine=pos_origine+pas;  // ajoute 1 cran
         servo_rpi_180.write(pos_origine); // crée une impulsion   
    
         delay(delai_pas);//entre chaque positionnement    
    } // fin de for
    position_servo_180 = pos_origine;

}

void servo_120(int pos_origine, int pos_expected, int delai_pas) {

   int delta = pos_expected - pos_origine;
   int delta_abs = abs(delta);
   int pas = delta/delta_abs;

   for (int i=0; i< delta_abs;i++) {  // défile n positions pour atteindre l'angle final     
         pos_origine=pos_origine+pas;  // ajoute 1 cran
         servo_rpi_120.write(pos_origine); // crée une impulsion   
         
         delay(delai_pas);//entre chaque positionnement    
    } // fin de for
    position_servo_120 = pos_origine;
}




  
                          
 

  

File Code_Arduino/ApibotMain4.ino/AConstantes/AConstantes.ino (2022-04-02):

//**CONSTANTES GENERALES**

//**CONSTANTES COMMUNICATION **

int nombreReception = NULL;//nombre (parametre) en reception
long params[10] ;//tableau des parametres sous la forme :
//[sensMotG,sensMotD,vitMotG,vitMotD,RotationCam,ElevationCam,RotationBras,ElevationBras,
//AvArBras,PinceBras]
int caractere;// caractere unitaire recu sur le port serie
int i =0;//compteur de parametres recus
int stock;//detection des virgules(2 a suivre ou pas)


//**CONSTANTES MOTEURS**

int sensG =0;// variable sens moteur gauche
int sensD= 0;// variable sens moteur droit
int vitG =0; // variable vitesse moteur gauche
int vitD =0; // variable vitesse moteur Droit


    //  Déclaration des broches PWM moteur(analogique)
    const int VITESSE_G=11; // broche vitesse moteur gauche (E1)
    const int VITESSE_D=9; // broche vitesse moteur droit (E2)
    
    //  Déclaration des broches moteur numeriques
    const int SENS_MOTG=10; // broche sens rotation moteur gauche (M1)
    const int SENS_MOTD=8; // broche sens rotation moteur droit (M2)
    

//**CONSTANTES CAMERA**

int CamHB =60; //variable angle Camera haut/bas
int CamRot =60; // variable angle Camera rotation
int vitesseCam=50;//vitesse de positionnement des servos

// positions extremes des servos
const int MinHB=550; // largeur impulsion en µs correspondant à la position min du servo camHB
const int MaxHB=2250; // largeur impulsion en µs correspondant à la position max du servo camHB
const int MinRot=550; // largeur impulsion en µs correspondant à la position min du servo camRot
const int MaxRot=2250; // largeur impulsion en µs correspondant à la position max du servo camRot


    //Déclaration des broches 
    const int CameraHB=2; // broche servo camera haut/bas
    const int CameraRot=3;//broche servo camera rotation
    
    //declaration d'objets servos
    Servo ScamHB;
    Servo ScamRot;

//**CONSTANTES BRAS**

int BrasPince = 0;// variable pince
int BrasAvAr = 0; // variable bras avant/arriere
int BrasElev = 0; // variable bras elevation
int BrasRot = 0; // variable bras rotation
int vitesseBras=50;//vitesse de positionnement des servos

    //Déclaration des broches
    const int BPince=8;//Broche servo pince
    const int BAvAr =9;//Broche servo bras Avant/arriere
    const int BElev =10;//Broche servo bras elevation
    const int BRot = 11; //Broche servo bras rotation

int valeurs[10] = {sensG,vitG,sensD,vitD,CamHB,CamRot,BrasPince,BrasAvAr,BrasElev,BrasRot};
// tableau regroupant les differentes valeurs.




// Declaration constantes diverses

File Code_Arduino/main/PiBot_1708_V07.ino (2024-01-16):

// Auteur du Programme : Luc DOMANGE - Tous droits réservés
//  31/07/2017.

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
//____________________________________________________________________________________
//                                                                                    !
// CE PROGRAMME EST RÉALISÉ POUR PILOTER DEUX MOTO-RÉDUCTEURS A CC DU RASPIBOT        !
// D'UNE FAÇON FLUIDE AUTANT QUE POSSIBLE AFIN DE SOULAGER CETTE PETITE PIGNONERIE EN !
// COMPORTANT DES RAMPES D'ACCÉLÉRATIONS ET DE MÉMORISATION DES PARAMÈTRES            !
// AFIN DE PASSER D'UN ÉTAT CE COMMANDE À UN AUTRE EN RESTANT TOUJOURS FLUIDE.        !
//____________________________________________________________________________________!

// Hypothèse : les moteurs sont branchés - en cablage- de telle sorte que la commande LOW ou 0 (zéro)
// fassent tourner les deux moteurs pour une marche Avant suivant la normalisation 
// du tutorial "Motor Control Pins" du driver L298, page 19/22 du "moteur-et-Cde-moteur-CC-2.pdf".

// Afin de facilité l'utilisation d'un connecteur 4 broches, sur l'Arduino, il serait souhaitable d'utiliser les pines
// 6 et 7 pour les commandes PWM (0 à 255)
// 8 et 9 pour les commandes numériques de sens de rotation (0 - 1) !
// Ici, les pines 10, 11, 12 et 13 sont utilisées pour des leds d'aide à la mise au point et le fun.
// Ne clignotent pas encore en fonction de la vitesse !

// Pour plus de fluidité, la base du programme a été de choisir une vitesse nominale par rapport au centre de gravité de l'essieu.
// Cette vitesse nominale est accélérée par incréments  de 25, (ou 5 ou 1 à venir) points sur 255 suivant le choix.
// Dans ce cas, la vitesse est incrémentée et est mémorisé le cas échéant.
// Cette vitesse est utilisée quelque soit le mouvement "Avant,", "Arrière", "Tout Droit", "Vire", "Toupie".

// THIERRY a dégrossi le travail par son programme.
// L'avantage de pratiquer de la sorte en gardant constemment en mémoire la vitesse nominale est de permettre des commandes fluides 
// et de ne pas avoir à choisir des valeurs numériques aléatoires qui seraient brutales pour la mécanique.

// La vitesse des moteurs est relié sur la vitesse nominale par un rapport "rX" , soit (vitesseX = vitesse_nominale * rX).
// Dans tous les cas, les vitesses moteurs restent entre 0 et 255.

// En ligne droite r=1, 
// Pour virer, la vitesse d'un moteur est augmentée d'autant qu'elle est diminuée pour l'autre
// par le produit (rG=rG * 1.1) et (rD = rD * 0.9) ou inverssement.
// Dans ce cas, plus on vire, plus r est multiplié à la puissance n pour 1.1 et 0.9 
// ou inverssement pour redresser et tourner dans l'autre direction.
// Les rX restent toujours mémorisés quel que soit le sens de rotation des moteurs.

// Pour sortir d'un virage, la fonction "Tout Droit" remet donc le rapport r = 1 tout en gardant la meme vitesse nominale.

// Une fonction "Toupie" est installée par rapport au centre de gravité de l'essieu.

// Une fonction "Impulsion" permet un accostage doux pour la préhention d'objets.
// Cette fonction est valide au dessous d'un seuil de vitesse basse, garde le sens ainsi que le rapport r donc la courbure du virage.

// Et évidemment la fonction "STOP" placée en première fonction met V à 0, le driver L298 n'est donc plus sollicité.

// Construction du programme : Reprendre les définitions des clefs de commandes sur les Notes S_Pen du SAMSUNG LDO
// Des lettres sont affectées pour les différentes actions écritent clairement dans le programme.
// Le clavier numérique est également utilisé en parallèle et bien défini dans le programme
// afin d'avoir toutes les clefs en un seul endoit.

// La communication serie est réalisée par un Serial.read et envoye le ou les caractères frappés par un "Line Feed",
// ce qui est génant pour une bonne fluidité.
// A modifier afin d'envoyer au fur et à mesure de la frappe.

// Cette version 5 utilise le terminal de l'Arduino directement par le cable 
// ou par la commande wifi à l'aide du RaspberryPI et VNC.
// Une version à venir utilisera pyqt4 en commandes graphiques


// Une version à venir en Python avec pyqt4!
// Programmes *.ui, *.py, *Main.py, combinant clavier ASCII, et graphique combos et curseurs etc...


// 170722, version 1, construction de la structure du programme afin de créer des fonctions répétitives simples, "void".
// 170723, Cette version 2 englobe la communication avec le terminal et d'une façon fluide 
// pour une ligne droite AV et AR, + vite et - vite (accélération gamma) et STOP.
// 170725, version 3, ajout des fonctions VIRAGES "Vire Gauche", "Vire Droite", rG et rD étant déjà installés dans le calcul des vitesses,
// ajout de la fonction Toupie.
// 170726, version 5, ajout pavé numérique pour plus de facilité des comandes mouvements sous une main.
// Ajout de la fonction "Impulsion".
// Mise en forme.
// 170730 Version 6, ajout de fonctions venant des touches actionnées dans while-if pour plus de flexibilités.
// et "ATTENDRE" dans l'état, c'est à dire, attendre x_milisecondes avant de valider une nouvelle commande.
// 170823 Version 7, mises au point V06 plus RAZ Vitesses
//__________________________________________________________________
//
//**********************  D E C L A R A T I O N S   ****************

//  Déclaration des constantes moteur numériques
const int E1 = 5; // cde vitesse PWM moteur de Gauche (6 futur)
const int E2 = 6; // cde vitesse PWM moteur de Droite (7  futur)

const int M1 = 4; //moteur de Gauche, cde LOW pour marche Avant, cde HIGH pour marche Arrière (8 futur)
const int M2 = 7; //moteur de Droite, cde LOW pour marche Avant, cde HIGH pour marche Arrière (9 futur)
//                 LOW ou 0, HIGH ou 1

//  Déclaration des leds
int ledAVG = 10;
int ledARG = 11;
int ledAVD = 12;
int ledARD = 13;

int swledAVG; //switch led AVG
int swledAVD; //switch led AVD
int swledARG; //switch led AVG
int swledARD; //switch led AVD

//Déclaration des paramètres pour les moteurs
int vit_nom = 0;   //vitesse nominale, limitée de 0 a 255
int vit_nomM;
int vit_G;  //vitesse moteur de Gauche, limitée de 0 a 255
int vit_D;  //vitesse moteur de Droite, limitée de 0 a 255

char Ordre_Avant;
char Ordre_Arriere;
char Stop;

int g_plus = 25;   //relation avec accélère  (acc)
int g_moins = 25;  //relation avec décélère (dec)
int acc;     // accélère
int dec;     //décélère
int i;
int delta;
  
int sens_G;  // sens de rotation moteur Gauche (0 AV, 1 AR)
int sens_D;  // sens de rotation moteur Droit  (0 AV, 1 AR)


float rD = 1;      //rapport vitesse moteur Droite / vitesse nominale
float rG = 1;      //rapport vitesse moteur Gauche / vitesse nominale
               //NOTA : la vitesse de la roue exter ne dépassera jamais la référence maxi 255
float rGM = rG;  // mémorisation rG en cours
float rDM = rD;  // mémorisation rD en cours               

float vit_rG; // vit_rG = vit_nom * rG;
float vit_rD; // vit_rD = vit_nom * rD;
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

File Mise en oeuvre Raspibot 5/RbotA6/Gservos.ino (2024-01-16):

void Servos()
{
     servoTo(*objet[indice-4], params[indice], valeur, toVitesse); //on execute la nouvelle position
   String ( a) = ("le servo ") + String(indice) + (" tourne a ") + String(valeur) + "\n";
   Serial.print(a);

     params[indice] = valeur;
/* for (int i=0;i<6;i++){
     if ((params[i+4]!= NULL)&& (params[i+4]!=Memservos[i])) { //si une valeur est passee et differente de la valeur actuelle
       servoTo(*objet[i], Memservos[i], params[i+4], toVitesse); //on execute la nouvelle position
        Memservos[i] = params[i+4];//on memorise la nouvelle position        
     }//fin if
  }// fin for*/
}// fin void Servos


/*void ServosFin(){
  for (int i=0;i<6;i++){
      servoTo(*objet[i], Memservos[i], 60, toVitesse);
//    
  }//fin for
}//fin void ServosFin*/



//... Fonction de positionnement progressif du servomoteur pas à pas fixe de n degrés...

 void servoTo (Servo toServo, int fromAngle, int toAngle, int toVitesse)  {
  
    int delta=toAngle-fromAngle;  // variation d'angle
    int deltaA=abs(delta);//valeur absolue de la variation
    int pas = delta/deltaA;//creation d'un pas de + ou - 1
   
    for (int i=0; i< deltaA;i++) {  // défile n positions pour atteindre l'angle final     
         fromAngle=fromAngle+pas;  // ajoute 1 cran
         toServo.write(fromAngle); // crée une impulsion   
         delay(toVitesse);//entre chaque positionnement    
    } // fin de for

} // fin de la fonction servoTo

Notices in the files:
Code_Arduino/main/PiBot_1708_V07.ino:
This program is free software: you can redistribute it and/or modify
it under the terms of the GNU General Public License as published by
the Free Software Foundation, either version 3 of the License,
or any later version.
